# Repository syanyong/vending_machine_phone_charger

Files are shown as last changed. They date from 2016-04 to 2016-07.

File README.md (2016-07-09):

# README #

This repository keeps the whole of the Mobile Charger Vending Machine.

### Requirements ###
The machine contains one of coin insert, 4 mobile charger and 4 selects, 4 start/pause and 4 stop/reset button.

* Firstly, select mobile charger by push select button. 
* Secondly, insert coin that the 7 segment shall show the charging time.
* Thirdly, push the start button to start charging that the relay shall be energized, and 7 segments shall show the countdown timer.
* [*Not implemented*] While charging, if start button is pushed, the countdown timer shall pause, and relay shall de-energize.
* While charging, if the stop button is pushed, the countdown timer shall reset to 0, and relay shall de-energize.

### Components ###
* MCU: Arduino Nano
* I/O Expander: MCP23017
* 7 Segment Driver: MAX7219

### Design Description ###
Arduino nano is selected because there is the lowest cost of Arduino. However, the I/O is not enough to provide the many buttons, so I use an I/O expander to solve this problem. The 4 digits 7 segment must be driven by scanning technique. In terms of programming, I have to make forloop for drive it that more CPU usage is taken. MAX7219 is the best solution by using SPI (Serial Peripheral Interface) to communicate with MCU.

### Author 
Sarucha Yanyong

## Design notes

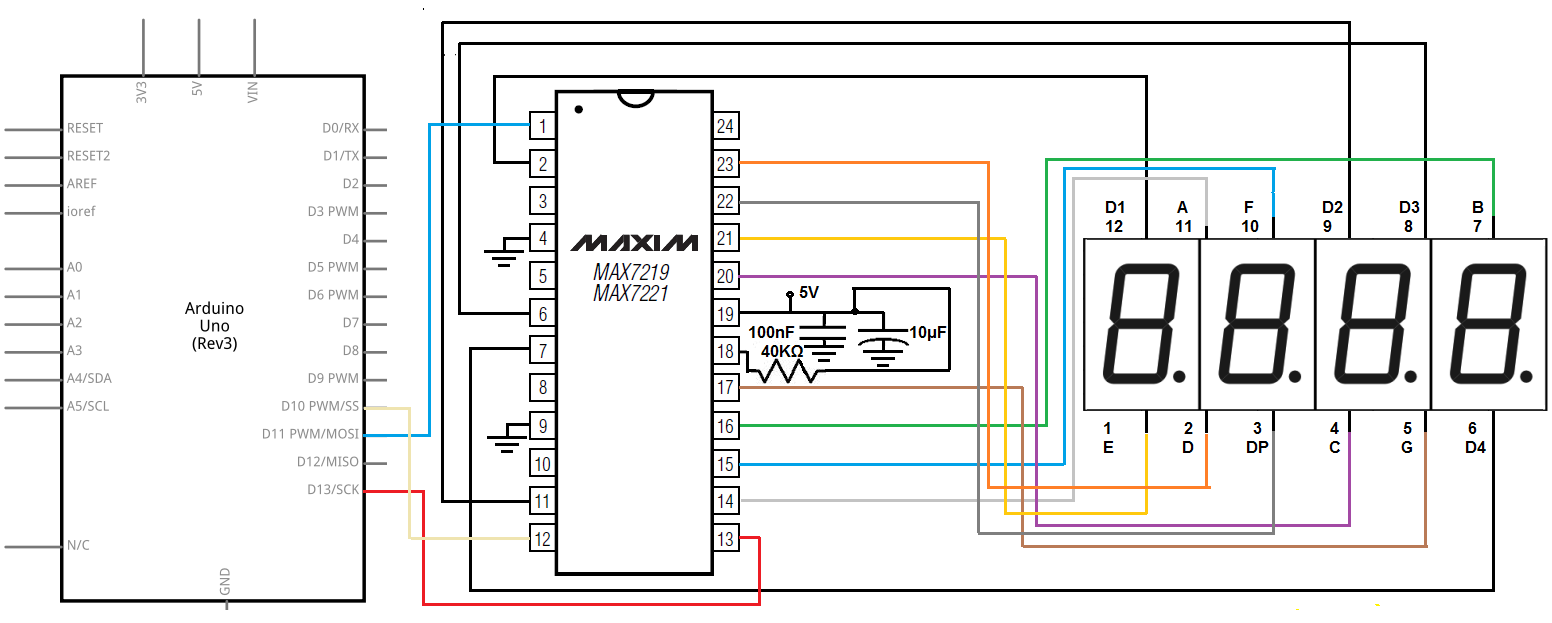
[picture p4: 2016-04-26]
document/ApplNote_MAX7219.png

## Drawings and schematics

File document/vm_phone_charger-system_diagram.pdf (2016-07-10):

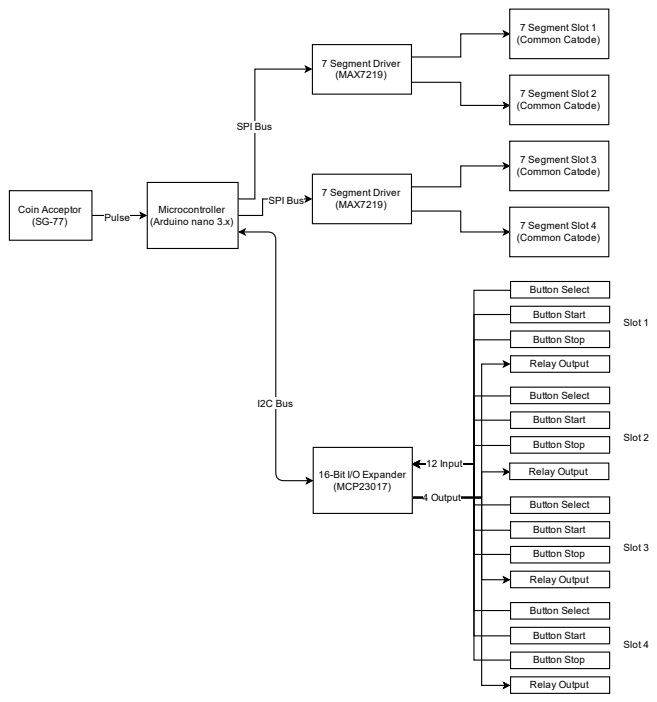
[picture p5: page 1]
SPI Bus; 7 Segment Driver (MAX7219); 4 Output; 16-Bit I/O Expander (MCP23017); Pulse; Coin Acceptor (SG-77); 7 Segment Slot 1 (Common Catode); 7 Segment Slot 2 (Common Catode); 7 Segment Slot 3 (Common Catode); 7 Segment Slot 4 (Common Catode); Button Select; Button Start; Relay Output; Button Stop; 12 Input; I2C Bus; Slot 1; Slot 4; Slot 2; Slot 3

SPI Bus Microcontroller
(Arduino nano 3.x)

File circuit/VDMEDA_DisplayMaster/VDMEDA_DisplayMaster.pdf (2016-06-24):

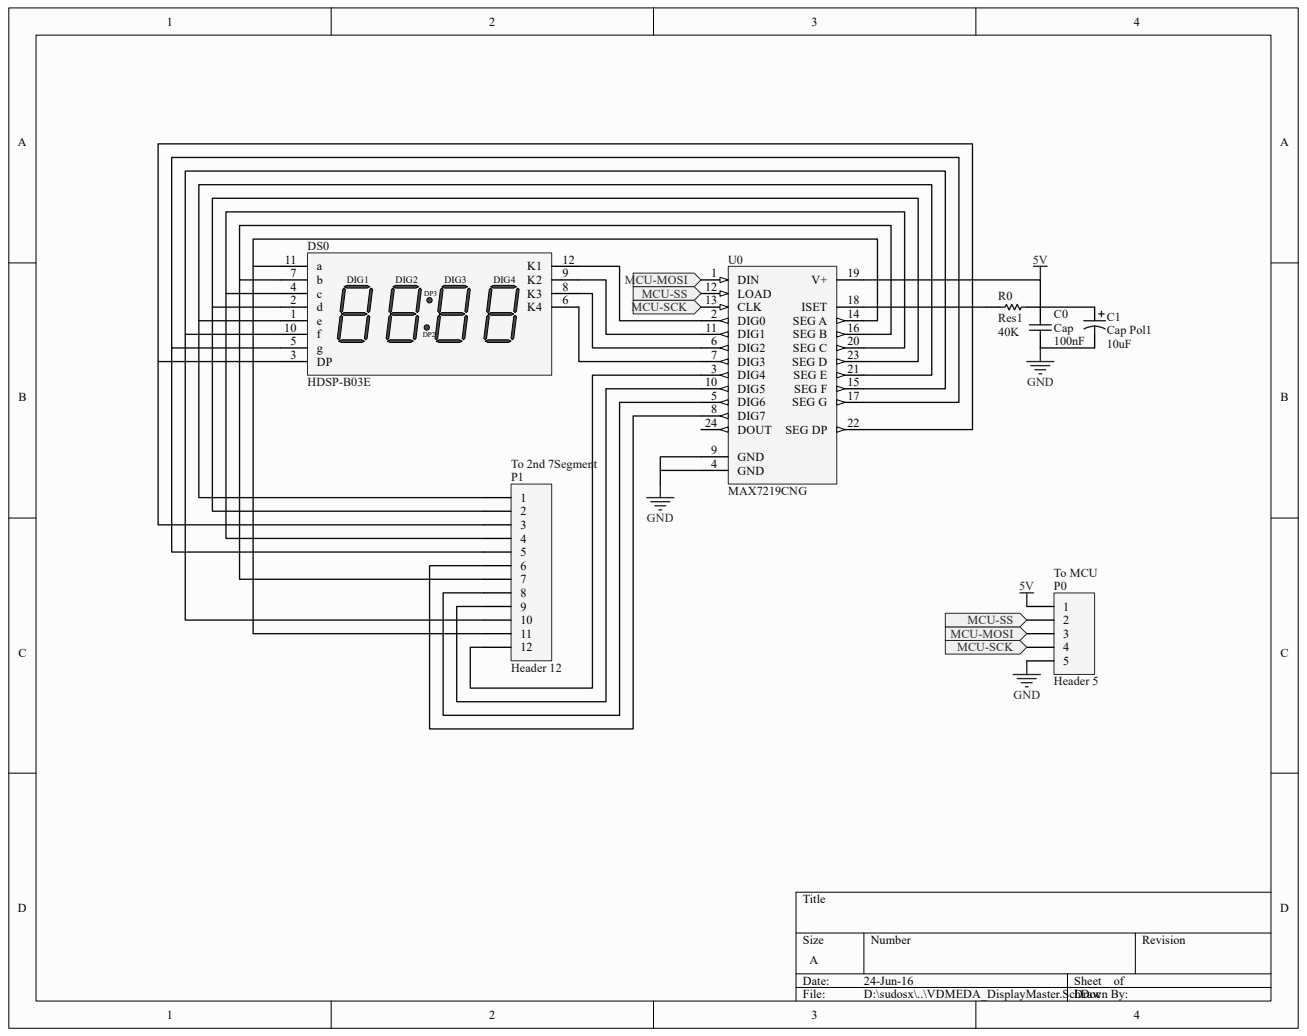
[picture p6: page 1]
Title; Size; Number; Revision; Date:; 24-Jun-16; Sheet of; File:; D:\sudosx\..\VDMEDA_DisplayMaster.SchDoc Drawn By:; DIG1; DIG2; DIG3; DIG4; HDSP-B03E; DIG2 6; DIG6 5; GND 4; SEG E; SEG G; ISET; SEG C; DIG4 3; SEG D; DIN 1; DIG0 2; SEG F; SEG B; 16 SEG A; GND 9; DIG1 11; DIG5 10; CLK 13; SEG DP; DIG3 7; DIG7 8 DOUT 24; LOAD 12; MAX7219CNG; Header 5; Header 12; C0 Cap; Cap Pol1; Res1; GND; MCU-MOSI MCU-SS MCU-SCK; MCU-MOSI; MCU-SS; MCU-SCK; To MCU; To 2nd 7Segment

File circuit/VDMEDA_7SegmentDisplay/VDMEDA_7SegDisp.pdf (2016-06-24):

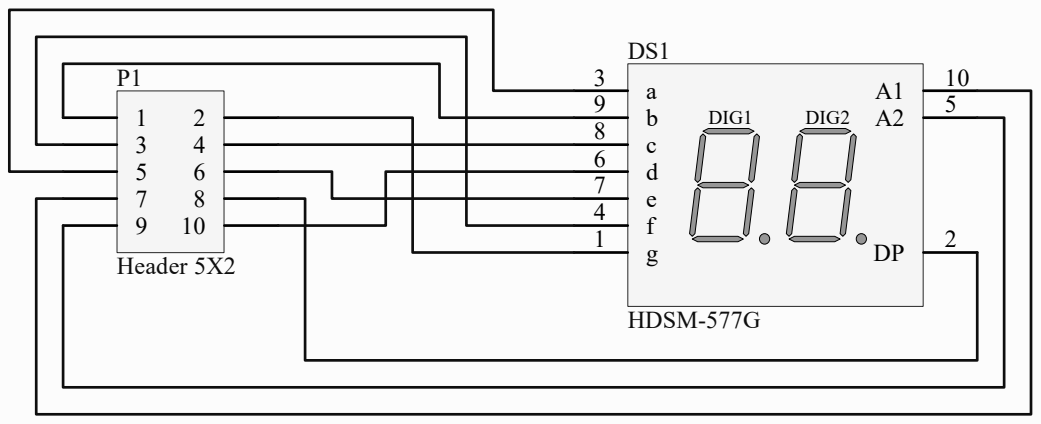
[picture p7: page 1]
Title; Size; Number; Revision; Date:; 25-Jun-16; Sheet of; File:; D:\sudosx\..\VDMEDA_7SegDisp.SchDocDrawn By:; DIG1; DIG2; HDSM-577G; Header 5X2

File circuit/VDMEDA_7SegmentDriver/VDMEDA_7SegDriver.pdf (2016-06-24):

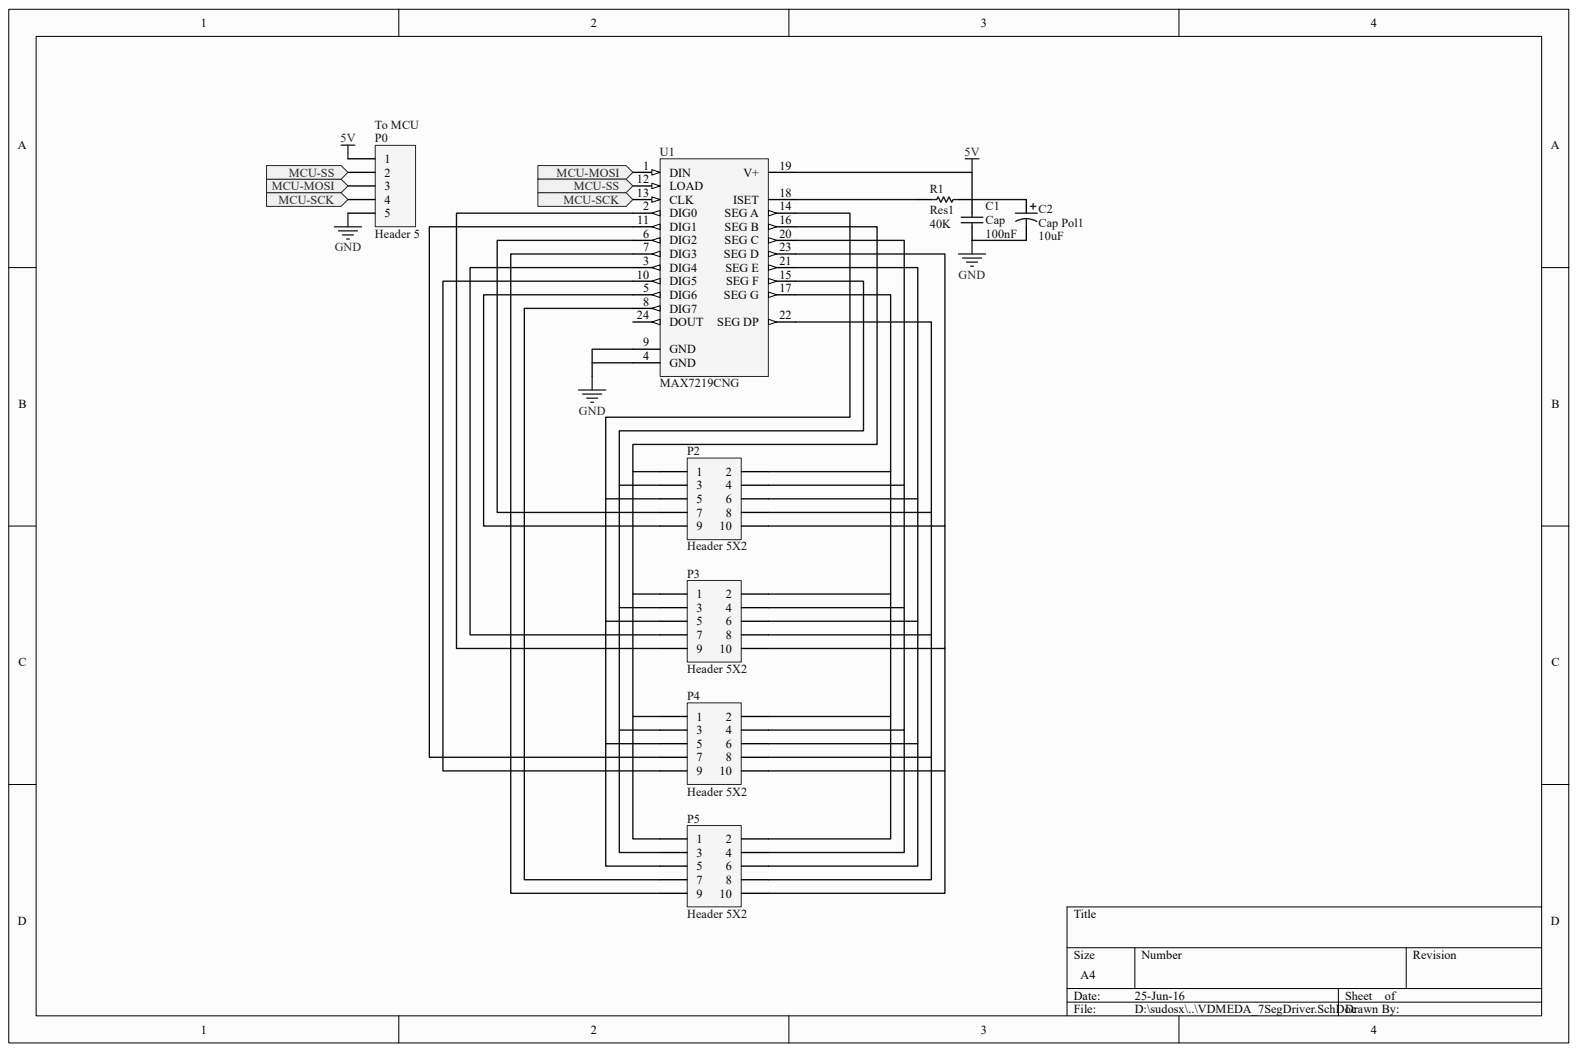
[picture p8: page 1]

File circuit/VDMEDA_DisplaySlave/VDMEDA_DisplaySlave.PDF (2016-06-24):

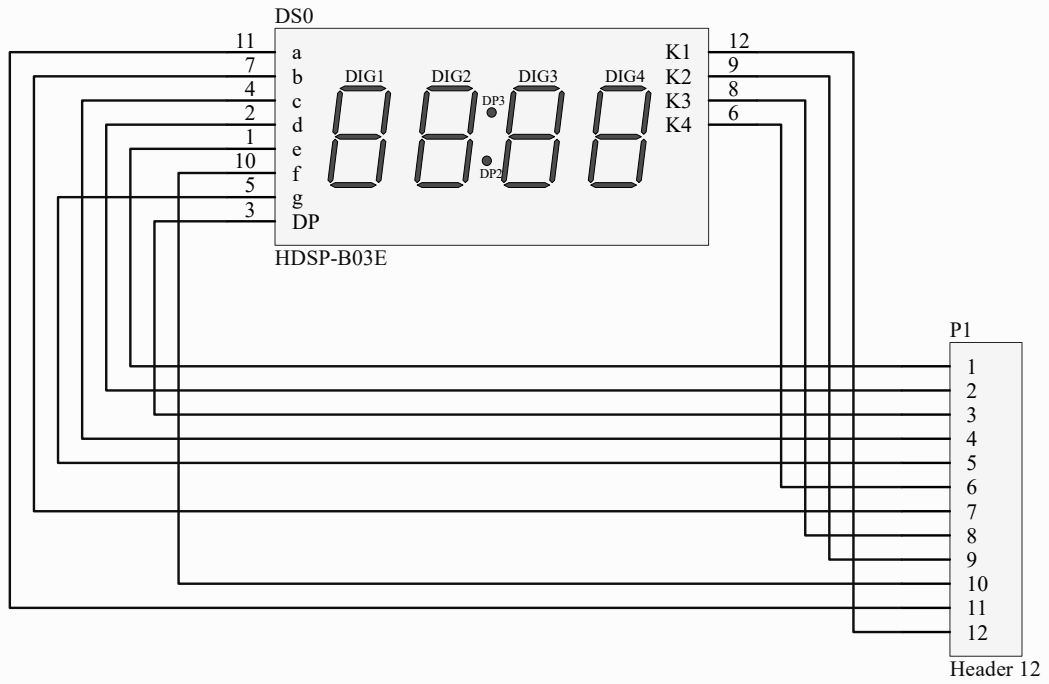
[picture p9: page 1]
Title; Size; Number; Revision; Date:; 24-Jun-16; Sheet of; File:; D:\sudosx\..\VDMEDA_DisplaySlave.SchDocrawn By:; DIG1; DIG2; DIG3; DIG4; HDSP-B03E; Header 12

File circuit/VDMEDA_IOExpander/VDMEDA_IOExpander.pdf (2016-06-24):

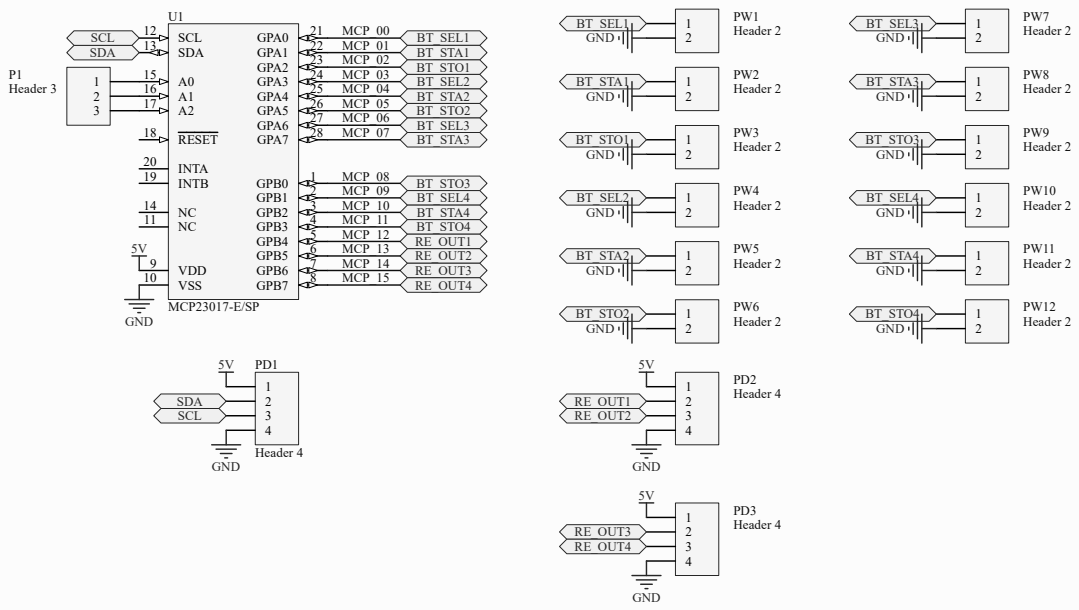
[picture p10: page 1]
Title; Size; Number; Revision; Date:; 24-Jun-16; Sheet of; File:; D:\sudosx\..\VDMEDA_IOExpander.SchDoc Drawn By:; GPB0; GPB1; GPB2; GPB3; GPB4; GPB5; GPB6; GPB7; 8 VDD; 9 VSS 10; SCL 12 SDA 13; RESET 18; INTB 19; INTA 20; GPA0; GPA1; GPA2; GPA3; GPA4; GPA5; GPA6; GPA7; MCP23017-E/SP; Header 4; GND; SDA SCL; SDA; SCL 321 P1; Header 3; PW1 Header 2; PW2 Header 2; PW3 Header 2; PW4 Header 2; PW5 Header 2; PW6 Header 2; PW7 Header 2; PW8 Header 2; PW9 Header 2; PW10 Header 2; PW11 Header 2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

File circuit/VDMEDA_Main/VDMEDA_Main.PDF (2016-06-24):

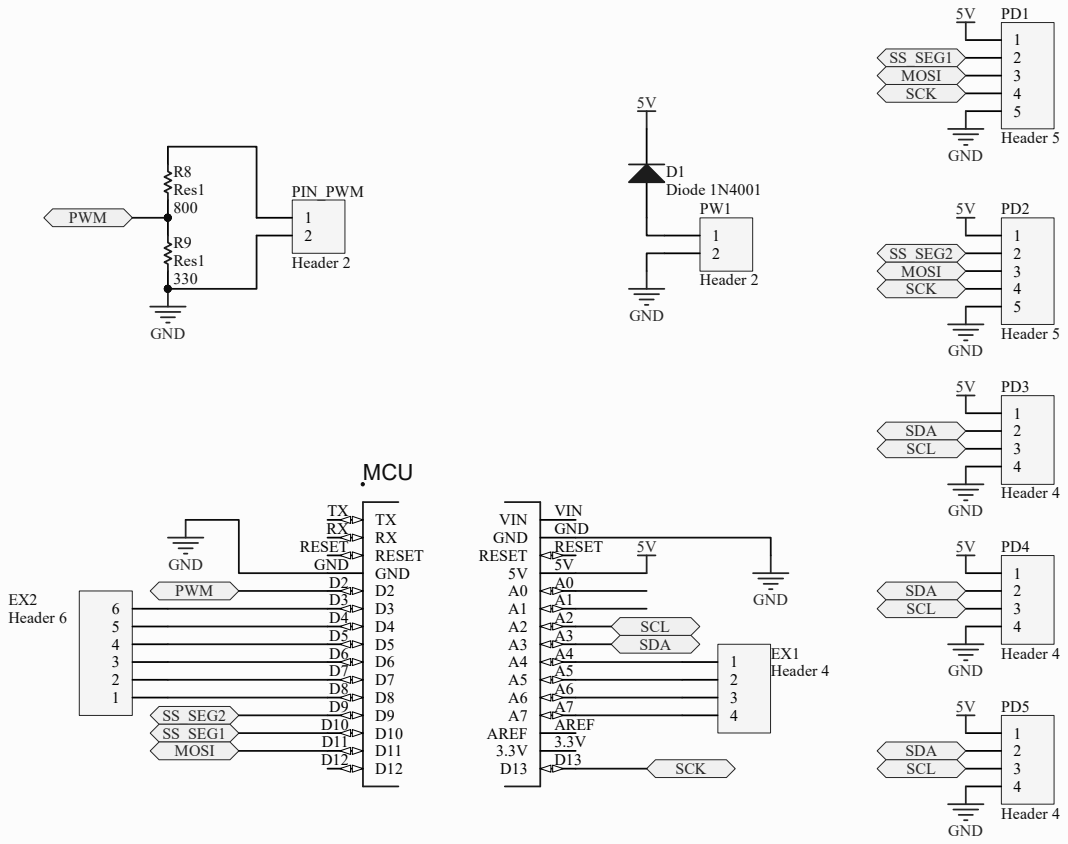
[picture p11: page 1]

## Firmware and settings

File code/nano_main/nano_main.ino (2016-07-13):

/* INCLUDE */
#include "SYLib_MAX7219.h"
#include "Adafruit_MCP23017.h"
#include "TimerOne.h"
// #include "stdio.h" // Debugging


/* DEFINE */
#define PIN_PWN       2

#define SEG1	1
#define SEG2	3
#define SEG3	2
#define SEG4	4

#define BT_SEL1    0
#define BT_STR1    1
#define BT_STP1    2

#define BT_SEL2    3
#define BT_STR2    4
#define BT_STP2    5

#define BT_SEL3    6
#define BT_STR3    7
#define BT_STP3    8

#define BT_SEL4    9
#define BT_STR4    10
#define BT_STP4    11

#define RELAY1		15
#define RELAY2		14
#define RELAY3		13
#define RELAY4		12

/* DECLARE */
Adafruit_MCP23017 mcp;


/* VARIABLE */
uint8_t coin = 0;
uint8_t pt_sel = 0;
uint8_t blink = 0;
char _pt[20];

uint8_t io_now[12];
uint8_t io_prv[12];
uint16_t disp[4];

uint8_t blink1 = 0;
uint8_t blink2 = 0;
uint8_t blink3 = 0;
uint8_t blink4 = 0;

uint8_t tim60sec = 0;
uint8_t tim1 = 0;
uint8_t tim2 = 0;
uint8_t tim3 = 0;
uint8_t tim4 = 0;

uint8_t is_ena1 = 0;
uint8_t is_ena2 = 0;
uint8_t is_ena3 = 0;
uint8_t is_ena4 = 0;


/* MAIN **************************************************/
void setup() {
		_delay_ms(4000);
		Serial.begin(9600);
		Serial.println("Hello World");

		setupMAX7219();
		setupIOExpander();
		setupIntTimer();
		setupIntExt();

} 

void loop() {
	/*
	 *  TASK: I/O Update
	 */
	getBTRel(mcp.readGPIOAB(), io_prv, io_now);
	printSeg(SEG1, disp[0]);
	printSeg(SEG2, disp[1]);
	printSeg(SEG3, disp[2]);
	printSeg(SEG4, disp[3]);
	// _printArr(io_now);
	

	/*
	 *  TASK: SELECTION
	 */
	if (io_now[BT_SEL1]) {
		coin = 0;
		pt_sel = 1;
	}
	else if (io_now[BT_SEL2]) {
		coin = 0;
		pt_sel = 2;
	}
	else if (io_now[BT_SEL3]) {
		coin = 0;
		pt_sel = 3;
	}
	else if (io_now[BT_SEL4]) {
		coin = 0;
		pt_sel = 4;
	}
	if (pt_sel == 1) {
		selectingScreen(SEG1, coin, &blink);
		disp[0] = coin;

		if (io_now[BT_STR1] == 1){
			tim1 = coin2Timer(coin);
			coin = 0;
			is_ena1 = 1;
			pt_sel = 0;
		}else if (io_now[BT_STP1] == 1){
			coin   = 0;
			pt_sel = 0;
		}
	}
	else if(pt_sel == 2){
		selectingScreen(SEG2, coin, &blink);
		disp[1] = coin;

		if (io_now[BT_STR2] == 1){
			tim2 = coin2Timer(coin);
			coin = 0;
			is_ena2 = 1;
			pt_sel = 0;
		}else if (io_now[BT_STP2] == 1){
			coin   = 0;
			pt_sel = 0;
		}
	}
	else if(pt_sel == 3){
		selectingScreen(SEG3, coin, &blink);
		disp[2] = coin;

		if (io_now[BT_STR3] == 1){
			tim3 = coin2Timer(coin);
			coin = 0;
			is_ena3 = 1;
			pt_sel = 0;
		}else if (io_now[BT_STP3] == 1){
			coin   = 0;
			pt_sel = 0;
		}
	}	
	else if(pt_sel == 4){
		selectingScreen(SEG4, coin, &blink);
		disp[3] = coin;

		if (io_now[BT_STR4] == 1){
			tim4 = coin2Timer(coin);
			coin = 0;
			is_ena4 = 1;
			pt_sel = 0;
		}else if (io_now[BT_STP4] == 1){
			coin   = 0;
			pt_sel = 0;
		}
	}
	else{

	}


	/*
	 *  TASK: STOP
	 */
	if (io_now[BT_STP1]){
		is_ena1 = 0;
		disp[0] = 0;
		tim1 = 0;
	}
	if (io_now[BT_STP2]){
		is_ena2 = 0;
		disp[1] = 0;
		tim2 = 0;
	}
	if (io_now[BT_STP3]){
		is_ena3 = 0;
		disp[2] = 0;
		tim3 = 0;
	}
	if (io_now[BT_STP4]){
		is_ena4 = 0;
		disp[4] = 0;
		tim4 = 0;
	}


	/*
	 *  TASK: DISPLAY COUNTER TIMER
	 */
	if (pt_sel != 1){
		disp[0] = tim1;
		if (tim1 > 0){
			scrShowRunning(SEG1, tim1, &blink1);
		}
	}
	if (pt_sel != 2){
		disp[1] = tim2;
		if (tim2 > 0){
			scrShowRunning(SEG2, tim2, &blink2);
		}
	}
	if (pt_sel != 3){
		disp[2] = tim3;
		if (tim3 > 0){
			scrShowRunning(SEG3, tim3, &blink3);
		}
	}
	if (pt_sel != 4){
		disp[3] = tim4;
		if (tim4 > 0){
			scrShowRunning(SEG4, tim4, &blink4);
		}
	}


	/*
	 *  TASK: TIMEOUT
	 */
	if (tim1 == 0){
		is_ena1 = 0;
	}
	if (tim2 == 0){
		is_ena2 = 0;
	}
	if (tim3 == 0){
		is_ena3 = 0;
	}
	if (tim4 == 0){
		is_ena4 = 0;
	}


	/*
	 *  TASK: DRIVER
	 */
	if (tim1 != 0){
		mcp.digitalWrite(RELAY1, LOW);
	}else{
		mcp.digitalWrite(RELAY1, HIGH);
	}
	if (tim2 != 0){
		mcp.digitalWrite(RELAY2, LOW);
	}else{
		mcp.digitalWrite(RELAY2, HIGH);
	}
	if (tim3 != 0){
		mcp.digitalWrite(RELAY3, LOW);
	}else{
		mcp.digitalWrite(RELAY3, HIGH);
	}
	if (tim4 != 0){
		mcp.digitalWrite(RELAY4, LOW);
	}else{
		mcp.digitalWrite(RELAY4, HIGH);
	}

}
/* FUNCTION **********************************************/
void selectingScreen(uint8_t seg, uint8_t data, uint8_t* blink_state){
	if (*(blink_state)){
		printSeg(seg, data);
	}else{
		printSegChar(seg, 3, 0xA);
	}
	_delay_ms(20);
	*(blink_state) = !*(blink_state);

}

void scrShowRunning(uint8_t seg, uint8_t data, uint8_t* blink_state){
	if (*(blink_state)){
		printSeg(seg, data);
	}else{
		printSegChar(seg, 0, 0xF);
		printSegChar(seg, 1, 0xF);
		printSegChar(seg, 2, 0xF);
		printSegChar(seg, 3, 0xF);
	}
	_delay_ms(20);
	*(blink_state) = !*(blink_state);	
}

void _printArr(unsigned char *arr){
	Serial.print("<");
	for (unsigned char i = 0 ; i < 12 ; i++){
		sprintf(_pt, "%d, ", *(arr+i));
		Serial.print(_pt);
	}
	Serial.print(">\n");
}

/*
 *	@brief: 
 */
void getBTRel(unsigned int io_in, uint8_t* io_prv, uint8_t* io_now){
	uint8_t ion;
	for (uint8_t i = 0 ; i < 12 ; i++) {
			ion = !( (io_in >> i) & 0x1); //Active Low
			// *(io_now+i) = ion;
			if ( (*(io_prv+i) == 1) && (ion == 0) ){
				*(io_now+i) = 1;
			} else{
				*(io_now+i) = 0;
			}
			*(io_prv+i) = ion;
 	}
}

void test7Seg(uint16_t* ts){
	printSeg(SEG1, *ts);
	printSeg(SEG2, *ts + 1);
	printSeg(SEG3, *ts + 2);
	printSeg(SEG4, *ts + 3);
	*ts = *ts +1;
	if (*ts >= 9990){
		*ts = 0;
	}
}

void testBT(){
	if (io_now[BT_SEL1]){
		printSeg(SEG1, 1);
	}
	else if (io_now[BT_STR1]){
		printSeg(SEG1, 2);
	}
	else if (io_now[BT_STP1]){
		printSeg(SEG1, 3);
	}

	if (io_now[BT_SEL2]){
		printSeg(SEG2, 1);
	}
	else if (io_now[BT_STR2]){
		printSeg(SEG2, 2);
	}
	else if (io_now[BT_STP2]){
		printSeg(SEG2, 3);
	}

	if (io_now[BT_SEL3]){
		printSeg(SEG3, 1);
	}
	else if (io_now[BT_STR3]){
		printSeg(SEG3, 2);
	}
	else if (io_now[BT_STP3]){
		printSeg(SEG3, 3);
	}

	if (io_now[BT_SEL4]){
		printSeg(SEG4, 1);
	}
	else if (io_now[BT_STR4]){
		printSeg(SEG4, 2);
	}
	else if (io_now[BT_STP4]){
		printSeg(SEG4, 3);
	}

}

/*
 * @brief: Coin to seconds.
 */
unsigned short coin2Timer(unsigned char coin){
    unsigned short out = 0;
    if ((coin >= 1) && (coin < 5)){
        out = coin*5;
    }
    else if ((coin >= 5) && (coin < 150)){
        out = coin*6;
    }
  else{
    out = 900;
  }
    return out;
}


void setupIOExpander(){
	mcp.begin();

	/*Input*/
	for (unsigned char i = 0; i <= 11; i++){
		mcp.pinMode(i, INPUT); 
		mcp.pullUp(i, HIGH);
	}
	/* Output */
	for (unsigned char i = 12; i <= 15; i++){
		mcp.pinMode(i, OUTPUT);
		mcp.digitalWrite(i, HIGH);
	}
}


void setupIntTimer(){
	Timer1.initialize(1000000);       // 1 Second
	Timer1.attachInterrupt(ISRCallback); // Attaches ISRCallback() as a timer overflow interrupt
}


void setupIntExt(){
	pinMode(PIN_PWN, INPUT);
	attachInterrupt(digitalPinToInterrupt(PIN_PWN), ISRCallbackExtInput, FALLING);
}


void ISRCallback()
{
	/* 1 sec */
	if (tim60sec++ > 60){
		if ((tim1 > 0) && (is_ena1==1)){
			tim1--;
		}
		if ((tim2 > 0) && (is_ena2==1)){
			tim2--;
		}
		if ((tim3 > 0) && (is_ena3==1)){
			tim3--;
		}
		if ((tim4 > 0) && (is_ena4==1)){
			tim4--;
		}
		tim60sec = 0;
	}
}


void ISRCallbackExtInput(){
	coin++;
}

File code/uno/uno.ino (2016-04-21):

// Brief: Vending Machine
// Platform: Arduino UNO
// Author: Sarucha Yanyong
#include "TimerOne.h"

// Define ------------------------------------------------- //
#define PIN_LED       13    // Built-in LED Pin
#define PIN_DATAIN    3
#define PIN_BT_START  4
#define PIN_BT_PAUSE  5
#define PIN_BT_STOP   6
#define PIN_OUT       13 // Relay = 7
#define BT_START      !digitalRead(PIN_BT_START)
#define BT_PAUSE      !digitalRead(PIN_BT_PAUSE)
#define BT_STOP       !digitalRead(PIN_BT_STOP)

// Variables -------------------------------------------- //
unsigned int targetSec = 0;
unsigned short pauseButtonFlag = 1;
volatile unsigned int coin = 0;
volatile unsigned int secCount = 0;
char buffer[20];

// Function --------------------------------------------- //
/* 
 *  @brief: Table for convert Coin to Second.
 */
int coin2Sec(int coin){
  return coin*2;
}

// MAIN ------------------------------------------------- //
void setup() {
  Serial.begin(9600);
  pinMode(PIN_LED, OUTPUT);
  pinMode(PIN_OUT, OUTPUT);
  pinMode(PIN_BT_START, INPUT);
  pinMode(PIN_BT_PAUSE, INPUT);
  pinMode(PIN_BT_STOP, INPUT);

  Timer1.initialize(1000000);       // 1 Second
  Timer1.attachInterrupt(callback); // A ttaches callback() as a timer overflow interrupt

  attachInterrupt(digitalPinToInterrupt(PIN_DATAIN), callbackExtInput, RISING);
}

void loop() {
  coin = 0;
  // Getting Coin
  Serial.println("READY");
  do{
    sprintf(buffer, "COIN %d\n", coin);
    Serial.write(buffer);
    if  (BT_STOP){
      coin = 0;
    }
  }while(!BT_START);
  sprintf(buffer, "GET COIN %d\n", coin);
  Serial.write(buffer);

  // Prepare
  targetSec = coin2Sec(coin);
  sprintf(buffer, "TARGET SEC %d\n", targetSec);
  Serial.write(buffer);
  
  // Countingdown
  secCount = 0;
  while( (!BT_STOP) && (targetSec != 0) ){
    sprintf(buffer, "COUNTING %d\n", secCount);
    Serial.write(buffer);

    // Drive Output as High
    if (!pauseButtonFlag) {
      digitalWrite(PIN_OUT, LOW);
    }else{
      digitalWrite(PIN_OUT, HIGH);
    }
    
    if (BT_PAUSE) {             // Pause
      while(BT_PAUSE);          // Wait for release.
      Serial.println("PAUSE");
      Serial.println(pauseButtonFlag);
      if (pauseButtonFlag) {
        Timer1.stop();
      }else{
        Timer1.resume();
      }
      pauseButtonFlag = !pauseButtonFlag;
    }

    if (secCount > targetSec){  // Timeout
      Serial.println("Timeout");
      break;
    }
    
  }
  // Drive Output as High
  digitalWrite(PIN_OUT, LOW);
  Serial.println("EXIT");
}

// Callback function
void callback()
{
  secCount++;
}

void callbackExtInput(){
  coin++;
}

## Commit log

2016-04-26 Add arduino Nano with MAX7219 as submodule.
2016-05-02 [Circuit] First release
    [VDMEDA_Arduino.PcbDoc, VDMEDA_Arduino.SchDoc, VDMEDA_Display1.PcbDoc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]
2016-05-12 Done display2 pcb
    [VDMEDA_Arduino.SchDoc, VDMEDA_Display1.PcbDoc, VDMEDA_Display2.PcbDoc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]
2016-05-12 Done display1
    [VDMEDA_Display1.PcbDoc]
2016-05-12 Improve wiring style of display 1 pcb
    [VDMEDA_Display1.PcbDoc]
2016-05-22 @Release Main Arduino Board.
    [VDMEDA_Arduino.PcbDoc, VDMEDA_Arduino.SchDoc]
2016-05-22 @Release Display 1, Main Arduino board is added signature.
    [VDMEDA_Arduino.PcbDoc, VDMEDA_Display1.PcbDoc]
2016-05-22 @Release 7Segment(Display2), adding signature.
    [VDMEDA_Display2.PcbDoc]
2016-05-25 @Release; Add pdf.
    [VDMEDA_Arduino.PcbDoc, VDMEDA_Display1.PcbDoc, VDMEDA_Display1.PrjPCB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]
2016-06-01 Circuit project config was updated.
    [VDMEDA_Display1.PrjPCB, VDMEDA_Display2.PrjPCB, VDMEDA_Main.PrjPcb]
2016-06-07 Added board overview.
2016-06-16 Fixed Display 1 circuit.
    [VDMEDA_Display1.PcbDoc, VDMEDA_Display1.PrjPCB, VDMEDA_Display1.SchDoc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]
2016-06-18 nano_prep is tested, all error have been solved.; Add nano_MCP23017 as submodule;
    [nano_prep.ino]
2016-06-19 Test timer with 7Segment. The result is pass.
2016-06-24 @Circuit; Add VDMEDA_7SegmentDisplay, VDMEDA_7SegmentDriver for 7 Segment 2 Digits.
    [VDMEDA_7SegDisp.PcbDoc, VDMEDA_7SegDisp.PrjPcb, VDMEDA_7SegDisp.SchDoc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]
2016-06-24 rename file
    [VDMEDA_7SegDisp.PrjPcb, VDMEDA_DisplayMaster.PrjPCB, VDMEDA_DisplaySlave.PrjPCB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]
2016-06-24 [Release Circuit]
    [VDMEDA_7SegDriver.PcbDoc, VDMEDA_7SegDriver.PrjPcb, VDMEDA_7SegDriver.SchDoc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]
2016-06-24 [Release-1.0.1] Remove unused file.
    [VDMEDA_Arduino.CSV]
2016-07-05 Code is tested. But counter timer is in second.
2016-07-08 [Release-1.1.0] nano_main.ino is main code that it has been update to reset coin when push bt_select.
    [SYLib_MAX7219.h, nano_main.ino, pseudo.c]
